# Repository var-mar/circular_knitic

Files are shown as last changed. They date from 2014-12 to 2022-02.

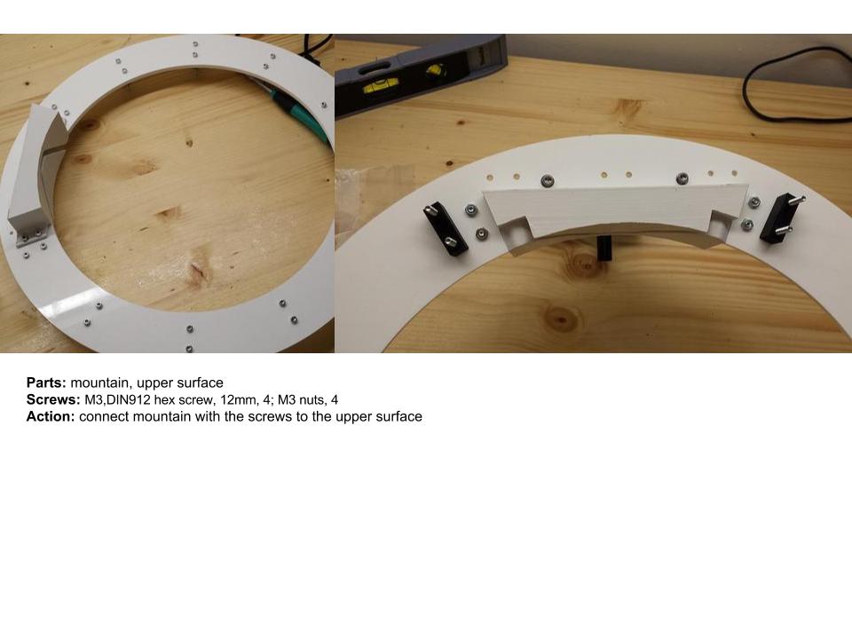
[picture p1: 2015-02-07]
workshop/CircularKniticTutorial/1.2 CK.jpg

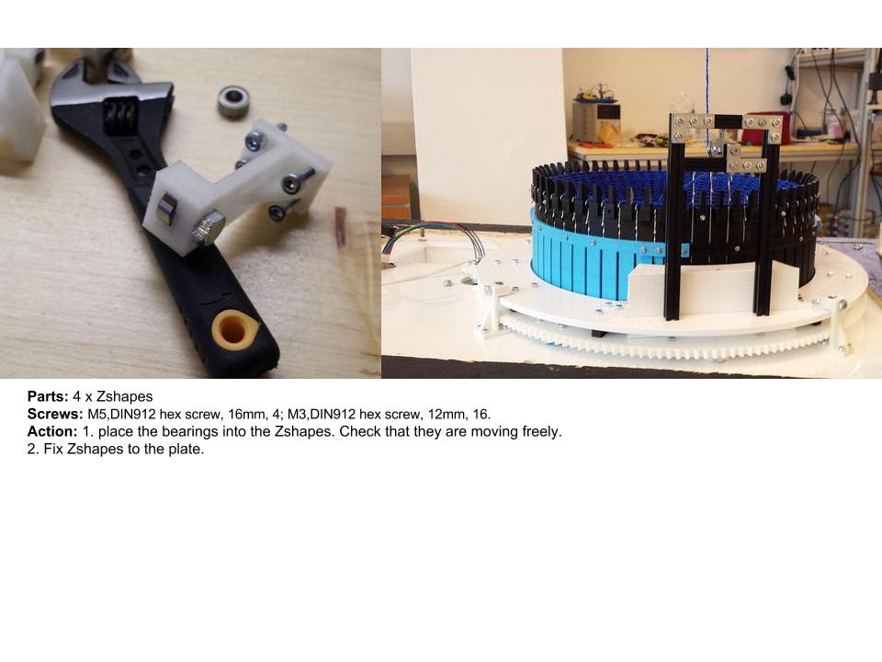
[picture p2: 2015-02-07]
workshop/CircularKniticTutorial/2.5 CK.jpg

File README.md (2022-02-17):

Circular knitic
===============

Circular Knitic, an open hardware knitting machine made by artist duo Varvara & Mar.  
* Project: https://var-mar.info/circular-knitic/ 
* Project video: https://www.youtube.com/watch?v=-GFXAGRynNM
* Instructables manual: www.instructables.com/id/Circular-Knitic/
* Manual with all pieces: http://issuu.com/marcanet/docs/circular_knitic_documentation

Brief history: This machine was done for the DOERS exhibition curated by David Cuartielles in Etopia Center for Art & Technology. We did an art intervention with 5 Circular Knitic machines, which were knitting for the time of the show (8 months). Hence, slowly the ceiling of art centre were covered with knitted tube garments. Each machine was knitting in different colour invading the exhibition space.

When building the machine, it is crucial to have the parts 3D printed precisely. Hence, print the parts in High Quality.
We have printed our machine with Ultimaker2, Makerbot Replicator 2, Makerbot Replicator 2x, and RepRapBcn+. Since reprap is not so preciase, some STL files are names as ...REP, which we have altered for that printer.

For laser cutting we have used 5mm and 6mm plexiglass. Use 6mm one for the gears, file gear-up.ai. For the rest use 5mm plexiglass. Important note, all plates are 600mm to 400mm, check you have select mm as unit. 

We are doing workshops to build one or more machines in one day, if you are interested hosting a workshop please let us know:
varvarag@gmail.com  or mar.canet@gmail.com See photos from WeMake Milano Makerspace workshop done in February 2015: https://www.flickr.com/photos/mcanet/sets/72157650274803049/

If you want to make a donation you can do in our PayPal account: varvarag@gmail.com 

To cite use:
```
@software{guljajeva_varvara_2014_6124168,
  author       = {Guljajeva, Varvara and
                  Canet Sola, Mar},
  title        = {Circular Knitic},
  month        = nov,
  year         = 2014,
  note         = {If you use this repository project, please cite it as below.},
  publisher    = {Zenodo},
  version      = {1.0.0},
  doi          = {10.5281/zenodo.6124168},
  url          = {https://doi.org/10.5281/zenodo.6124168}
}
```

We have publish some articles about this topic:
- Knitic - The Revolution of Soft Digital Fabrication. DH 2013: 497-499 [http://dh2013.unl.edu/abstracts/ab-173.html]

Opensourceecology had design some parts of the machine in parametric design in openscad:
https://wiki.opensourceecology.org/wiki/CircularKnitic_Parametric

Please send a photo if you build one machine to us we happy to make a gallery to all machines produced and a map with locations.

Copyright (c) 2014 Varvara Guljajeva & Mar Canet 

> THIS MATERIAL IS DISTRIBUTED AS IS WITH NO GUARANTEE OF FUNCTIONALITY OR RELEVANCE TO THIRD PARTY PROJECTS - THE DEVELOPERS ARE THUS NOT TO BE HELD RESPONSIBLE FOR PERSONAL INJURIES, HARDWARE, FINANCIAL, OR ANY OTHER LOSSES AND IN GENERAL FOR ANY MISFORTUNATE EVENT CAUSED BY THE DESCRIBED SOFTWARE/HARDWARE OR IN THE PROCESS OF ATTEMPTING TO IMPLEMENT IT. IF YOU DON'T AGREE WITH THE AFOREMENTIONED YOUR ARE NOT ALLOWED TO USE THE MATERIAL PROVIDED HEREIN

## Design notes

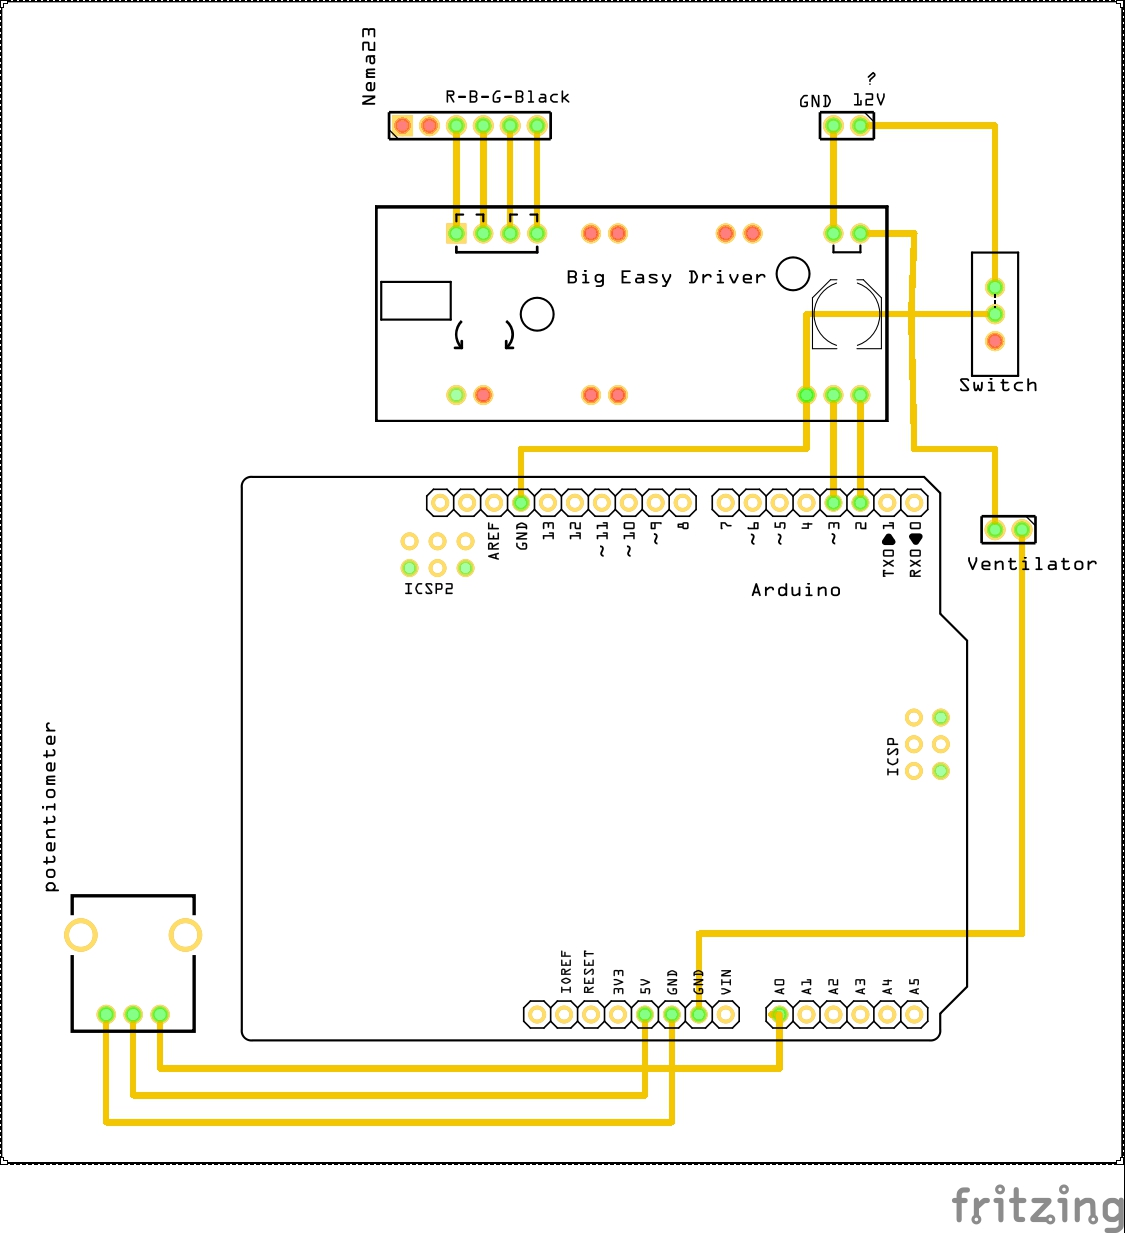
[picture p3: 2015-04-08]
Arduino/CKcircuitSchema_pcb.jpg

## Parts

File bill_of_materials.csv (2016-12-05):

Budget - Circular Knitic
description | real price | quantity | total | link
needles | €0.45 | 100 | €45.00 | http://www.bsk.co.uk/knitmastersilver-reed-sk120--sr120-xkn8-763-p.asp
stepper motor nema23 | €50.00 | 1 | €50.00
Big Easy stepper motor Driver | €20.00 | 1 | €20.00
Arduino Uno | €21.00 | 1 | €21.00
ventilator 12v 40mm x 40mm | €6.00 | 1 | €6.00
power supply 12v | €20.00 | 1 | €20.00
cabling | €8.00 | 1 | €8.00
carbon fiber tensor 2mm | €1.00 | 1 | €1.00 | http://www.mwmaterialsworld.com/es/barra-fibra-de-carbono.html
bearings (bore 5mm x 10mm x 4mm) | €0.60 | 14 | €8.40
screws and nuts | €10.00 | 1 | €10.00
shaft of motor | €7.00 | 1 | €7.00 | http://www.pololu.com/product/2675
switch | €4.00 | 1 | €4.00
paper clips | €0.01 | 30 | €0.30
Plexiglas 5mm | €10.00 | 2 | €20.00 | http://proplastik.ee
Plexiglas 6mm | €11.00 | 1 | €11.00 | http://proplastik.ee
filament | €38.00 | 1 | €38.00
makerbeam 150mm | €2.20 | 2 | €4.40
makerbeam 60mm | €0.80 | 3 | €0.80
makerbeam screws | €3.00 | 1 | €3.00
makerbeam Lshape | €0.90 | 5 | €4.50
wood structure | €25.00 | 1 | €25.00
claw weight | €6.00 | 4 | €24.00
paraphine | €2.00 | 1 | €2.00
 |  | Total | €334.00
Manufacturing
3d prints outers | €15.00 | 4 | €60.00
3d print inners | €6.00 | 24 | €144.00
3d print yarnholders | €12.00 | 4 | €48.00
3d print bearring holders | €3.00 | 5.00 | €15.00
3d print connectors | €1.00 | 15 | €15.00
Lasercutting | €90.00 | 0.5 | €45.00
 |  | Total | €327.00

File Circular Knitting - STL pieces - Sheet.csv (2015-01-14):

comments | max layer height | Order nr. | Components | # of Pieces
1 and 2 are the same pieces. | 0.06 (recommended) | 1 | BearringBig1212 (repaired).stl | 1
this piece has been made slightly bigger for the reprap printer | 0.15 | 2 | BearringBigREP (repaired).stl | 1
 | 0.06 | 3 | BearringSmall1312 (repaired).stl | 4
 | 0.15 | 4 | Pipe (repaired).stl | 1
 | 0.15 | 5 | YarnHolderPalo.stl | 2
6 and 7 are the same | 0.06 | 6 | Zshape1212 (repaired).stl | 4
made for reprap | 0.15 | 7 | ZshapeRep (repaired).stl | 4
 | 0.1 | 8 | connection0912.stl | 11
 | 0.06 | 9 | inner0112 (repaired).stl | 12
 | 0.1 | 10 | mountain1212 (repaired).stl | 1
 | 0.15 | 11 | outer2511 (repaired).stl | 4
 | 0.1 | 12 | outerNeedleConnector (repaired).stl | 4
 | 0.1 | 13 | yarnHolder0212 (repaired).stl | 4
*print all parts in 'High Quality' (the option that your slicr program has).
Max layer height 0.1mm and infill 15% or 20%.
With layer height 0.06 no filing is required

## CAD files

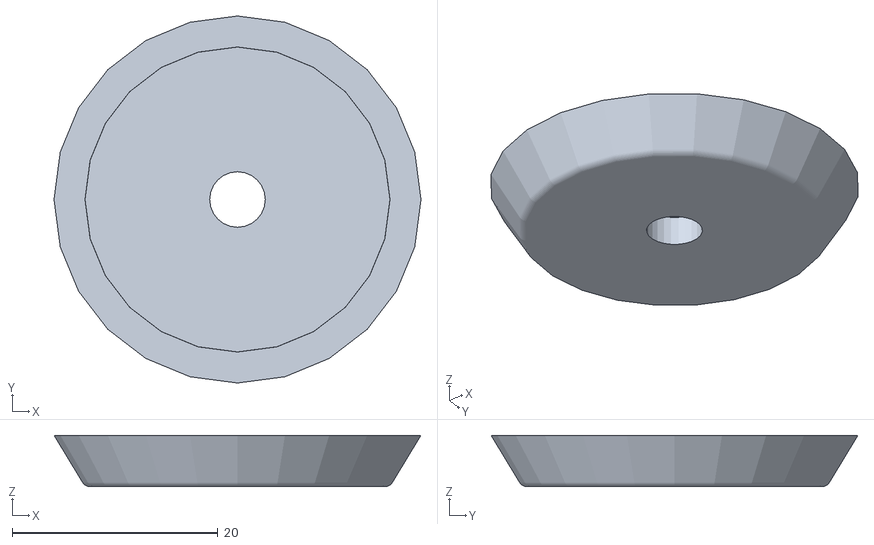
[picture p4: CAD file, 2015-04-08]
STLs/YarnTensioner/spring.stl
35.7 x 35.7 x 5.00

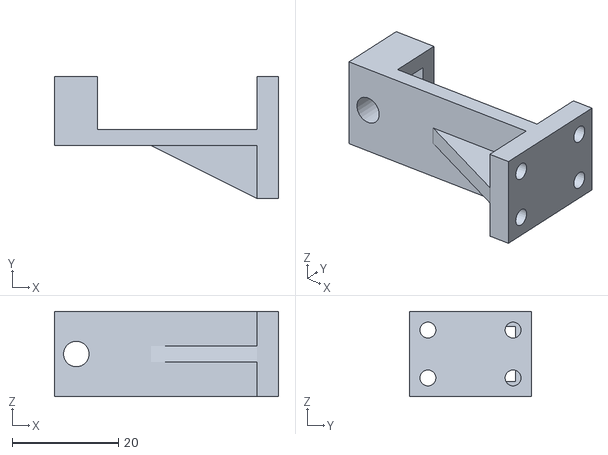
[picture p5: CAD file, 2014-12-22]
STLs/ZshapeRep_x_4.stl
42.1 x 23.0 x 16.0

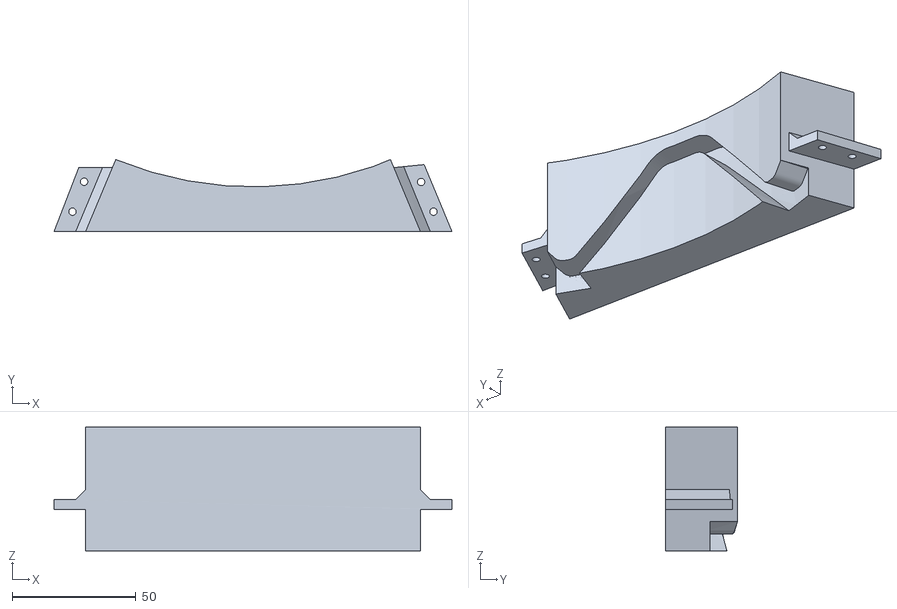
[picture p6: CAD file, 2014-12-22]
STLs/mountain1212 (repaired).stl
160.9 x 29.1 x 50.0

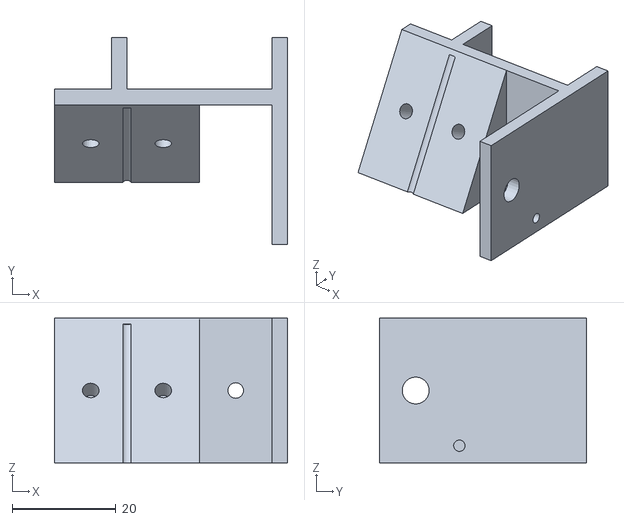
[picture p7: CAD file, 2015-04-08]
STLs/YarnTensioner/yarnfeederSupport.stl
45.0 x 40.0 x 28.0

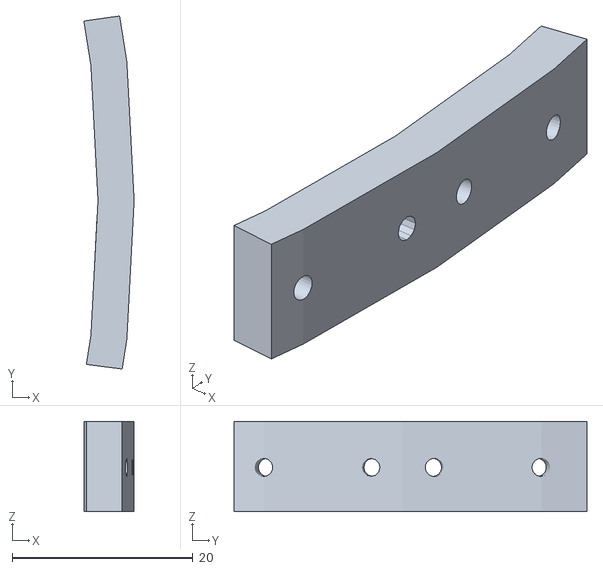
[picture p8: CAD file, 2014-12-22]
STLs/outerConnector_x_4.stl
5.57 x 39.1 x 10.0

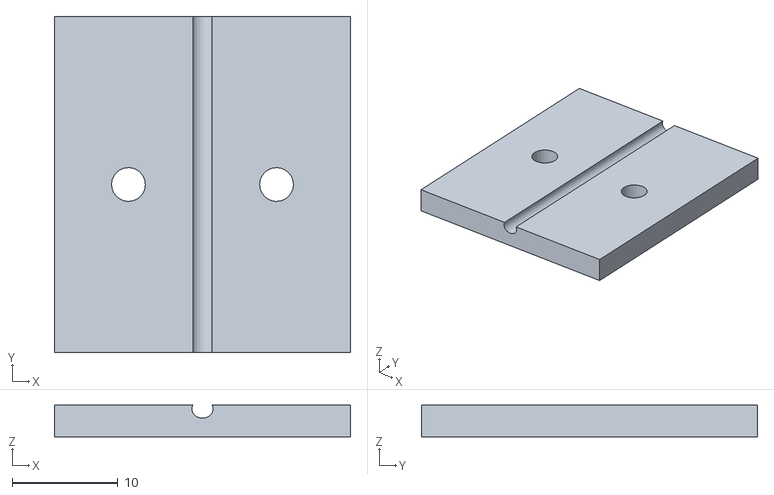
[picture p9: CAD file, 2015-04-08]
STLs/YarnTensioner/YarnTensonerHolder300315.stl
28.0 x 31.8 x 3.00

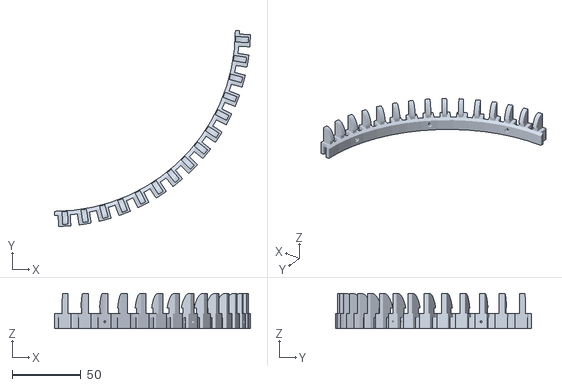
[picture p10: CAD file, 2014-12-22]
STLs/yarnHolder0212_x_4.stl
142.9 x 142.9 x 25.6

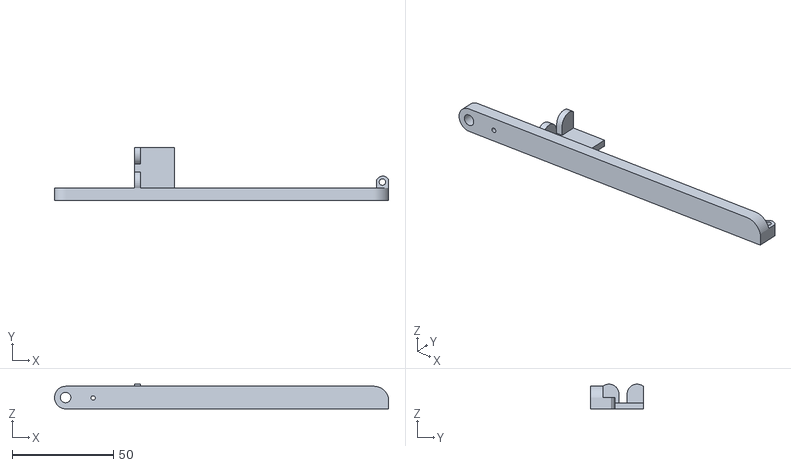
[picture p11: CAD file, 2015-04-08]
STLs/YarnTensioner/yarnTensioner1.stl
165.3 x 26.0 x 12.3

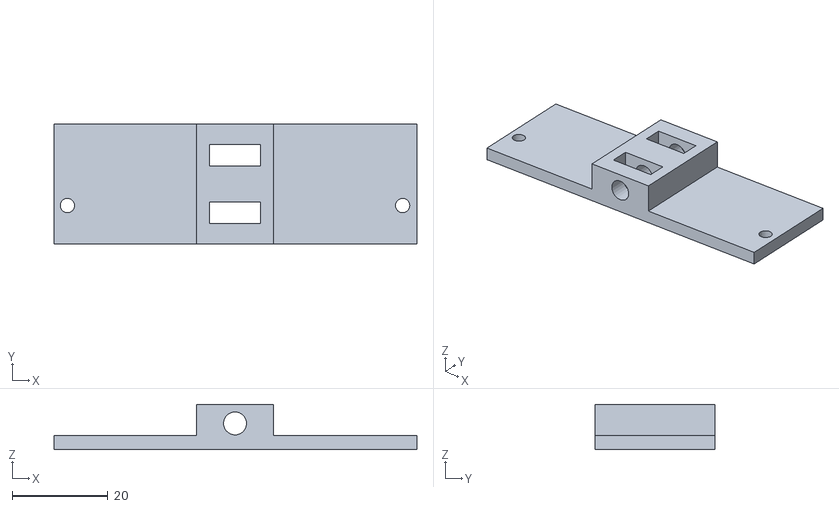
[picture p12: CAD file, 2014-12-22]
STLs/BearringBigREP (repaired).stl
75.8 x 25.0 x 9.50

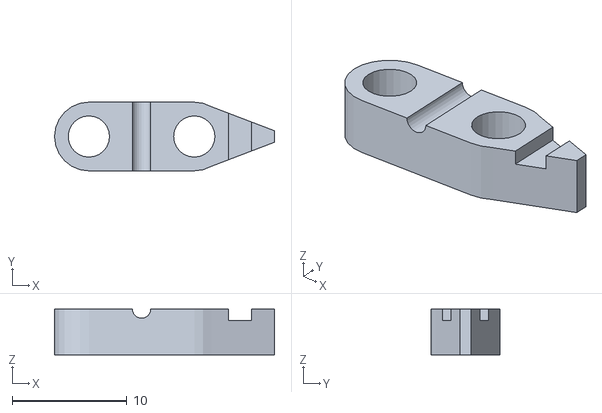
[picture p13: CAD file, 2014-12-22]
STLs/YarnTensioner/YarnHolderPalo.stl
19.2 x 6.00 x 4.00

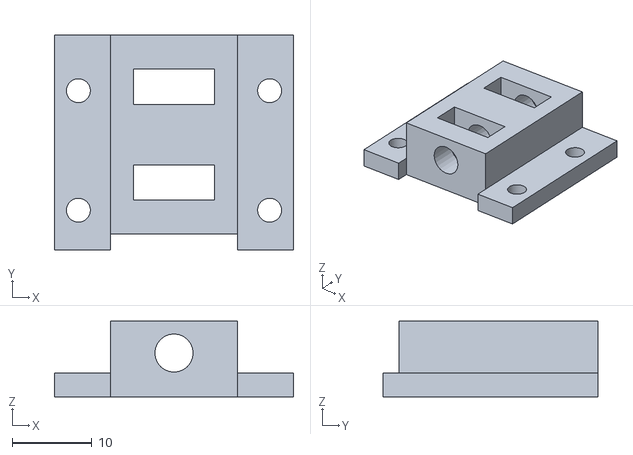
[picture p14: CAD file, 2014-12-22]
STLs/BearringSmall1312_x_4.stl
30.0 x 27.0 x 9.50

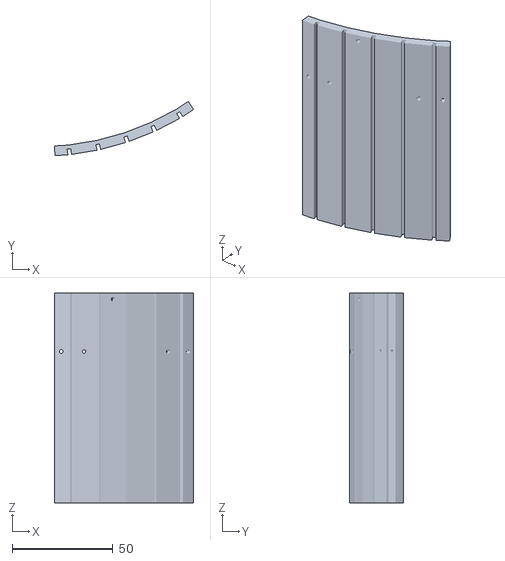
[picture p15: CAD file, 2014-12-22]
STLs/inner0112_x_12.stl
69.0 x 26.8 x 104.0

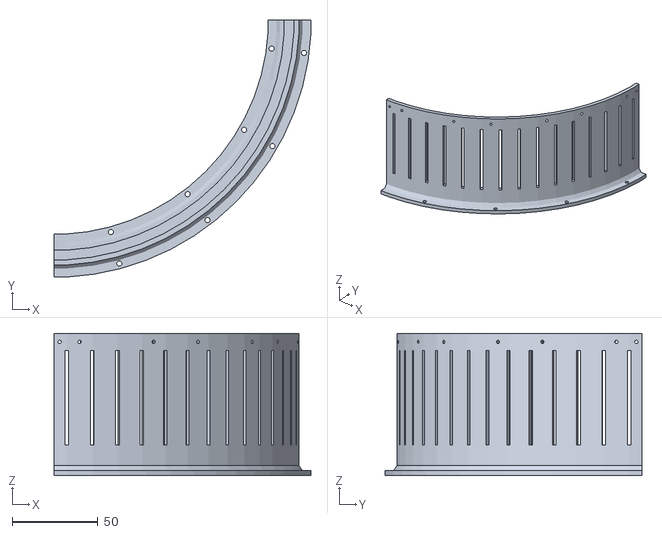
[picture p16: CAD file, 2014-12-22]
STLs/outer2511_x_4.stl
149.8 x 149.8 x 83.0

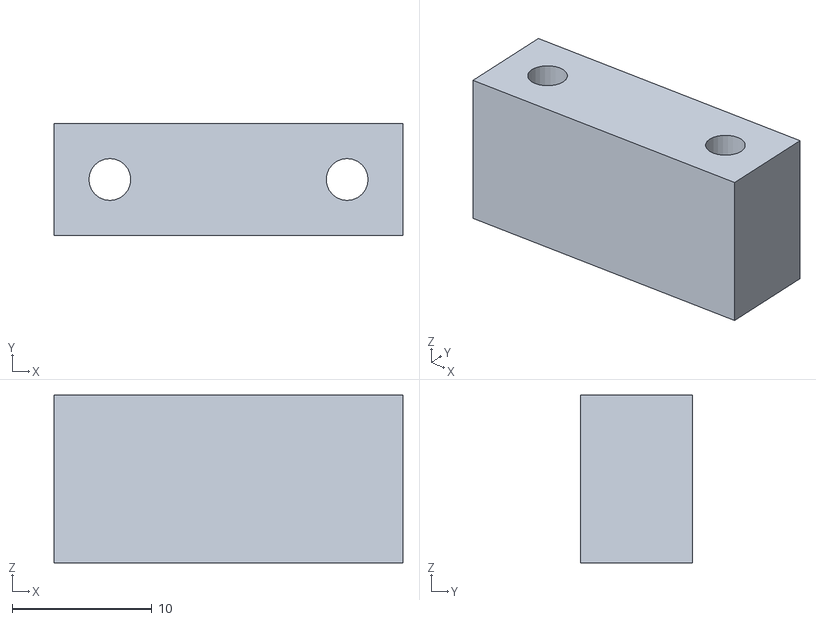
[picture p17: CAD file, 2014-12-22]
STLs/connection0912_x_11.stl
25.0 x 8.00 x 12.0

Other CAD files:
STLs/BearringBig1212 (repaired).stl
STLs/Zshape1212_x_4.stl
3D_model/CircularKnitic~.skp

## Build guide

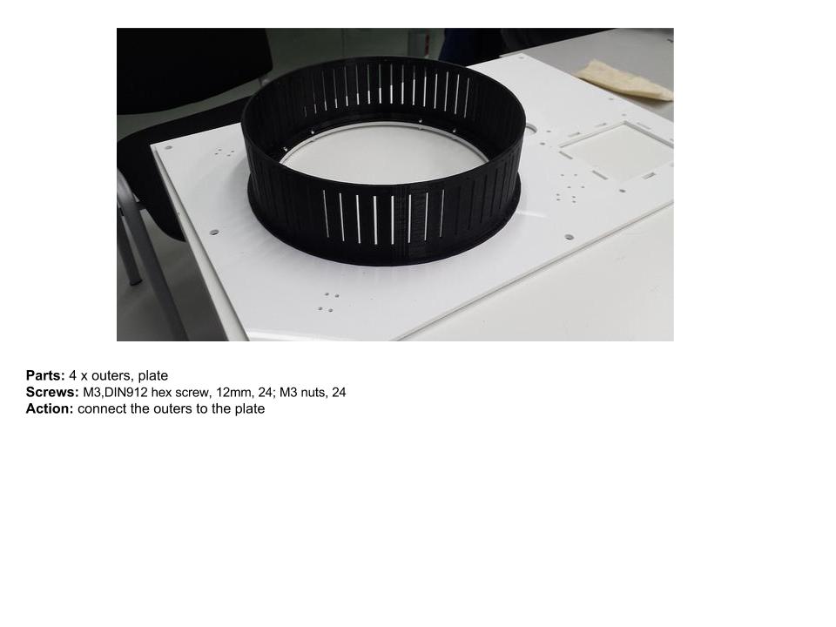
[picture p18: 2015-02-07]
workshop/CircularKniticTutorial/2.1 CK.jpg

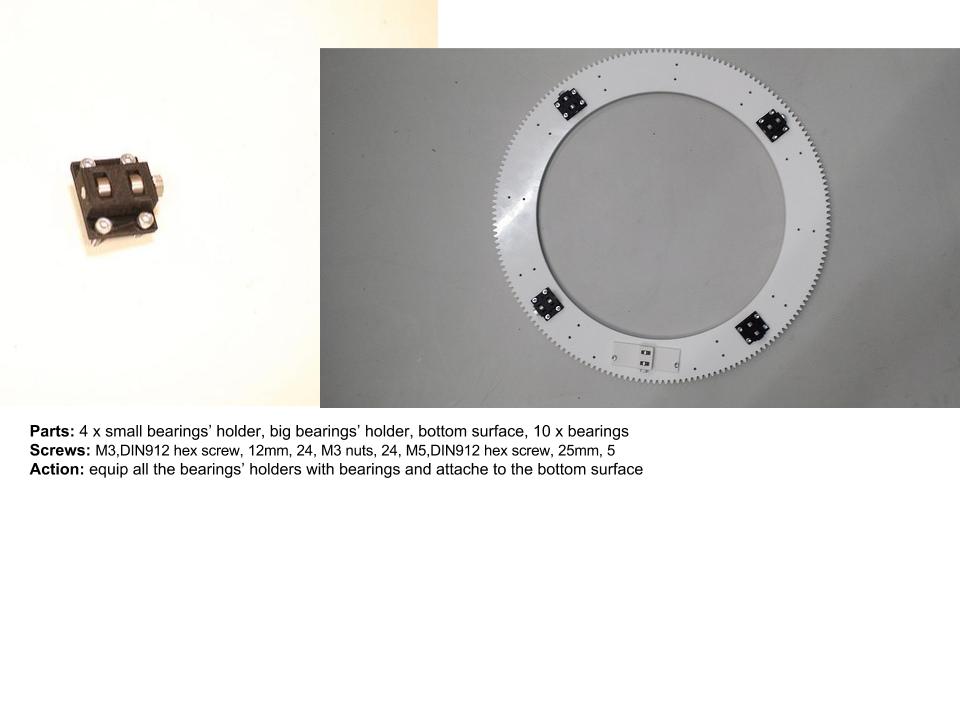
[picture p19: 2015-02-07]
workshop/CircularKniticTutorial/2.2 CK.jpg

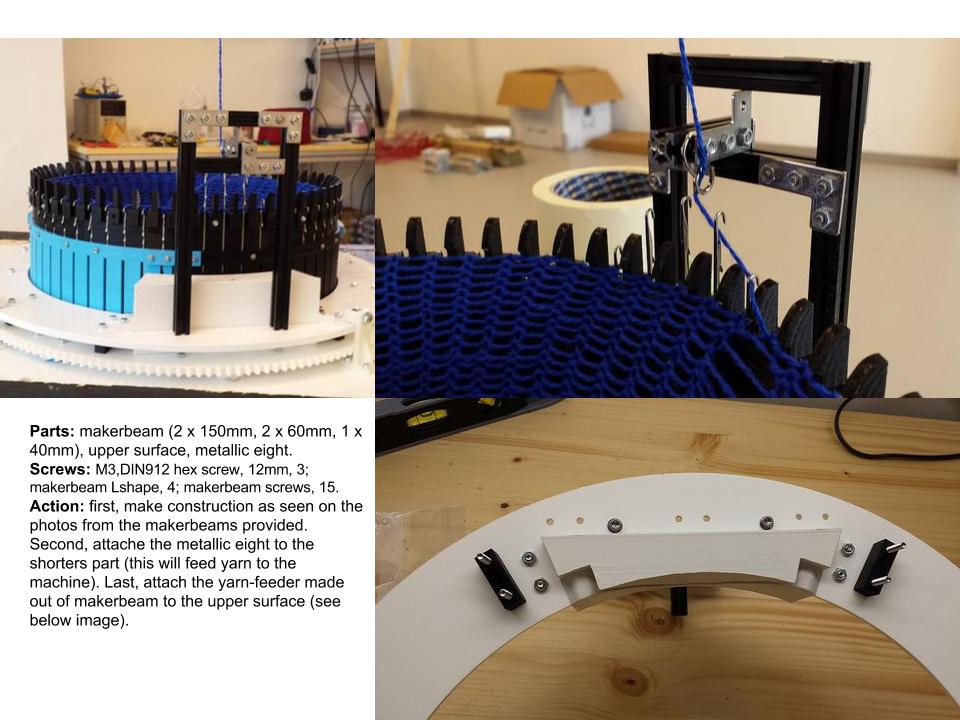
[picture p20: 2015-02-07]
workshop/CircularKniticTutorial/1.3 CK.jpg

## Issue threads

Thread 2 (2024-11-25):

Questions About Circular Knitic

serrarrs, 2024-11-25:
Hi Varvara and Mar,

I’m a master’s student at Hochschule Pforzheim in the Design and Future Making department, and as part of one of my projects, I’m working on creating the Circular Knitic. I have a few questions regarding the 3D printing and laser-cutting of some parts:

-Regarding the 3D printing, I noticed that the required layer height is quite thin, which significantly increases the printing time. Could you explain why such thin layers are necessary for this project?

-For the laser-cutting process, is there a specific offset value I should consider to achieve the correct thickness for the cuts?

-Lastly, about the plexiglass parts: can I use the same thickness (5mm) for all the components, or are there any specific parts that require a different thickness?

Thank you very much for your time and support :)
Best regards,
Serra

oujlaki, 2024-11-25:
hi!!
We are also students at the Free University of Bolzano, faculty of design and we have seen your beautiful project as a reference for our knitting machine. We are looking for the right needles. Could you give us some additional information? we understand that they are the master silver reed sk120 sr120, but I can't find them in the right size online.
waiting for your kind help,
best regards
karola

mcanet, 2024-12-04:
Hi,

The needle type is well-documented (Silver Reed SK120, SR120 LATCH NEEDLES 8mm). While other needle types can be used, they may require adaptations in the design. This particular needle is not the most common, but it is available for purchase on eBay or other platforms.
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
Screen shot from our manual: https://issuu.com/marcanet/docs/circular_knitic_documentation

High-precision 3D printing with a small layer height is required. You can experiment with lower resolution (larger layer heights), but this will depend on your 3D printing machine. Additionally, it may require extra sanding to assemble everything properly.

All plexiglass components can also be made with 5mm thickness.

We’d love to see photos if you build it!

Best regards,

Mar

serrarrs, 2024-12-09:
Hi,

Thank you for your answer! Is it possible to send the link to the motor you used? There are many versions of the Nema 23 motor, and I'm not sure which one is correct.

Best,
Serra

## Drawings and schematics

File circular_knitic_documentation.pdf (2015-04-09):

open source knitting machine
http://var-mar.info | http://www.knitic.com

Varvara Guljajeva & Mar Canet

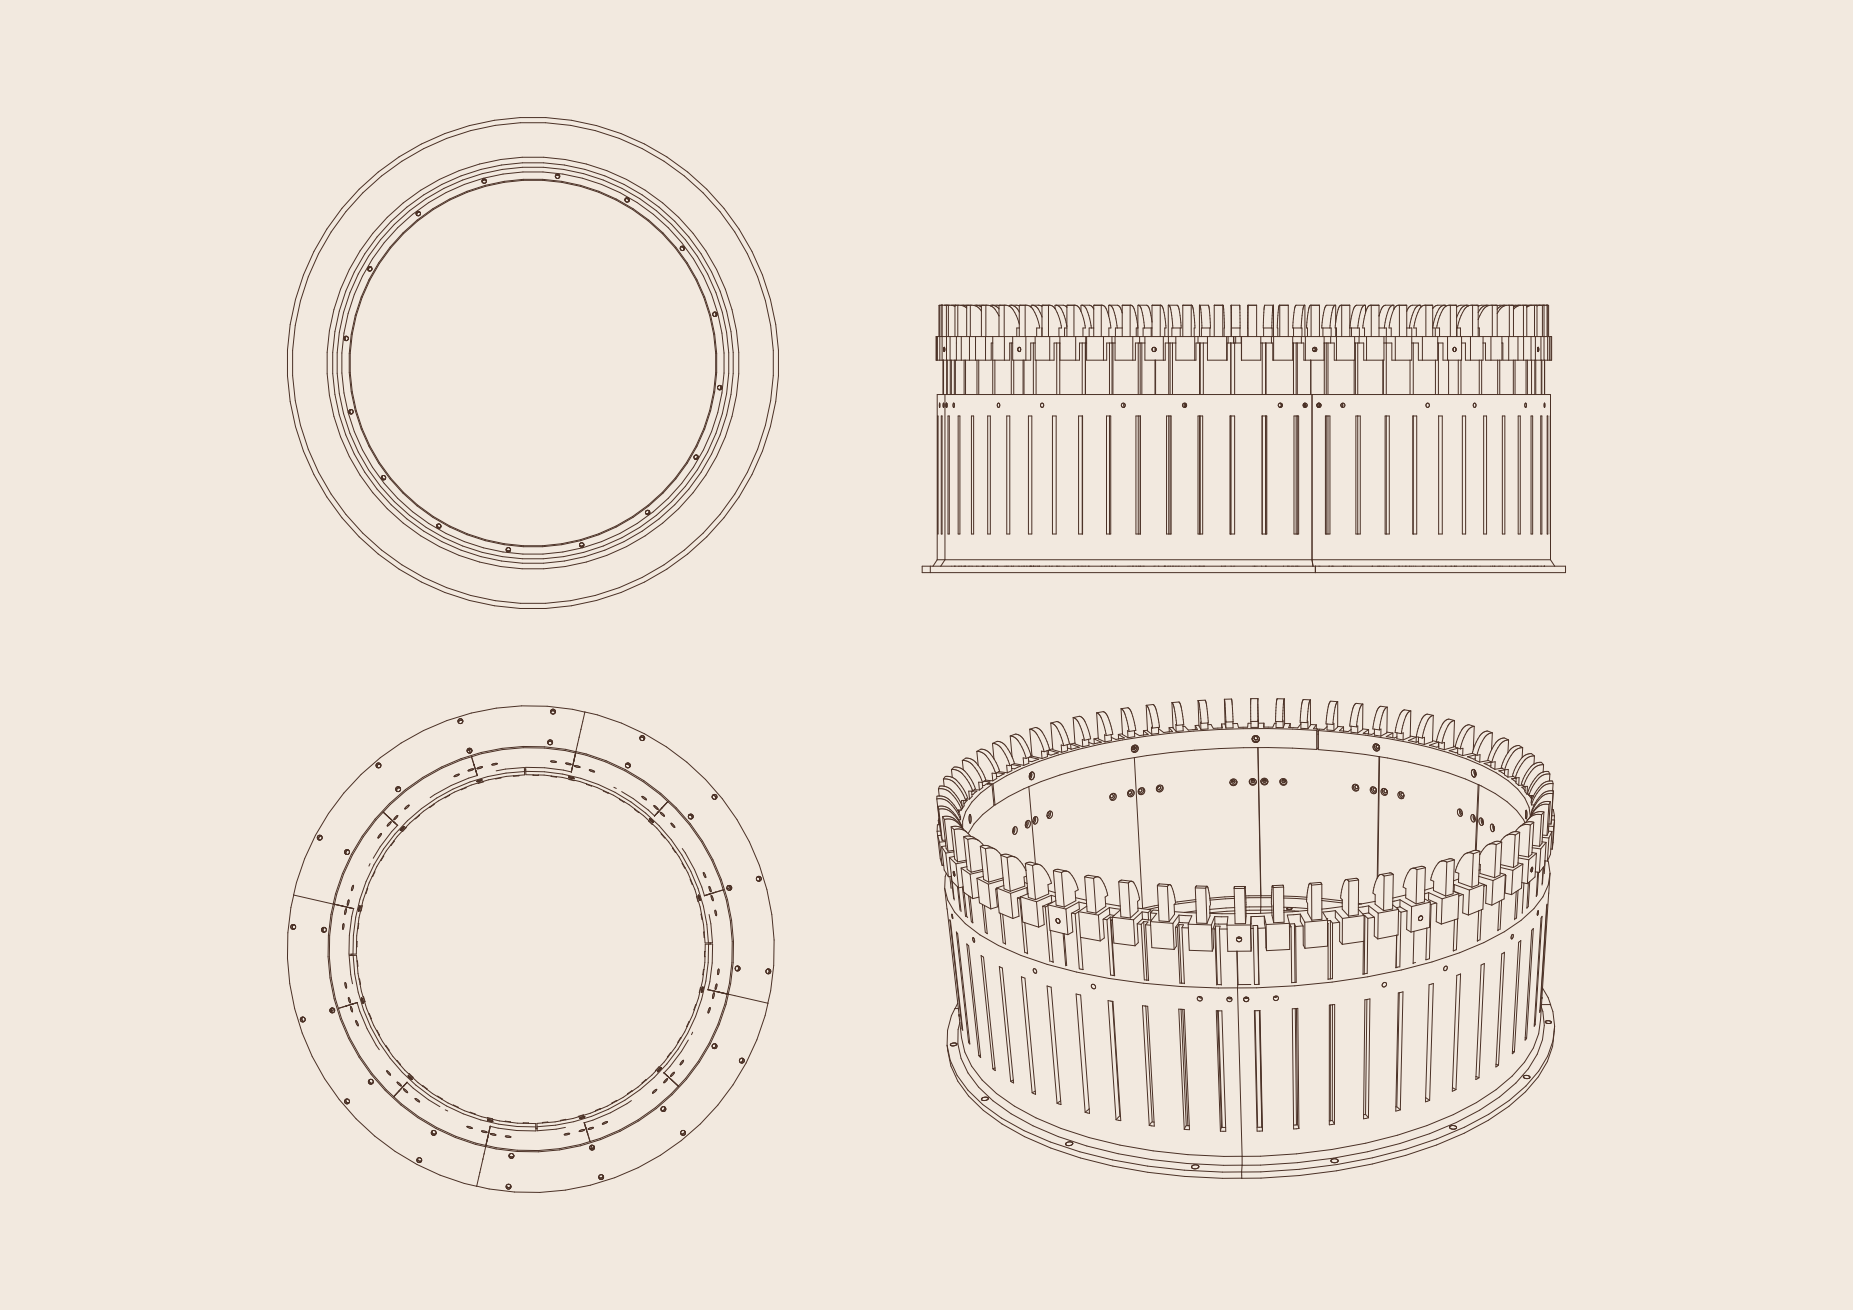
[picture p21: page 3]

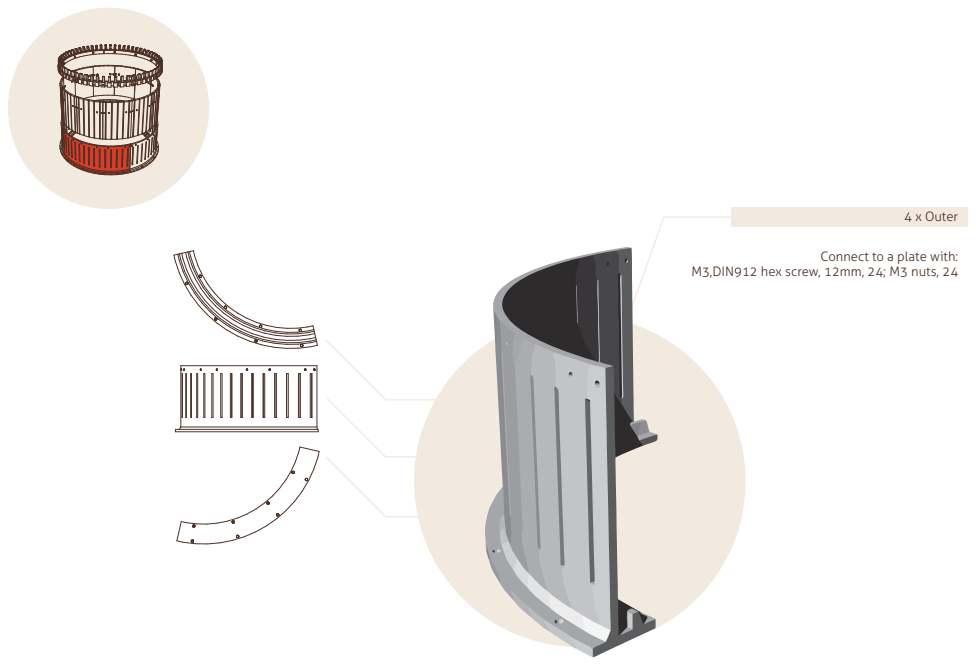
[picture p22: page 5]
4 x Outer

Connect to a plate with:

M3,DIN912 hex screw, 12mm, 24; M3 nuts, 24

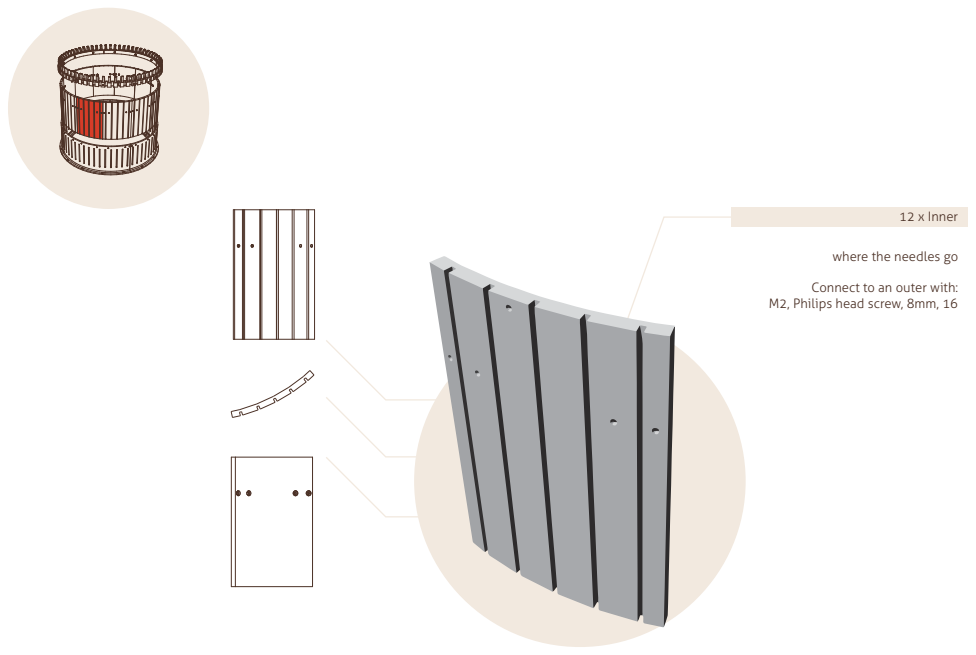
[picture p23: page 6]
12 x Inner

where the needles go

Connect to an outer with:
M2, Philips head screw, 8mm, 16

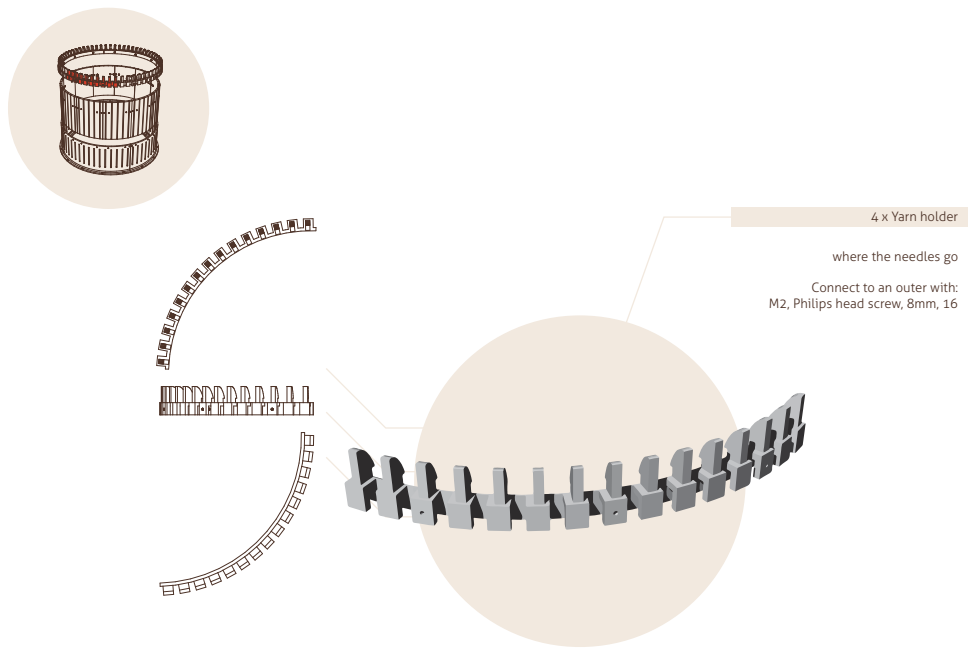
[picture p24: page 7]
4 x Yarn holder

where the needles go

Connect to an outer with:
M2, Philips head screw, 8mm, 16

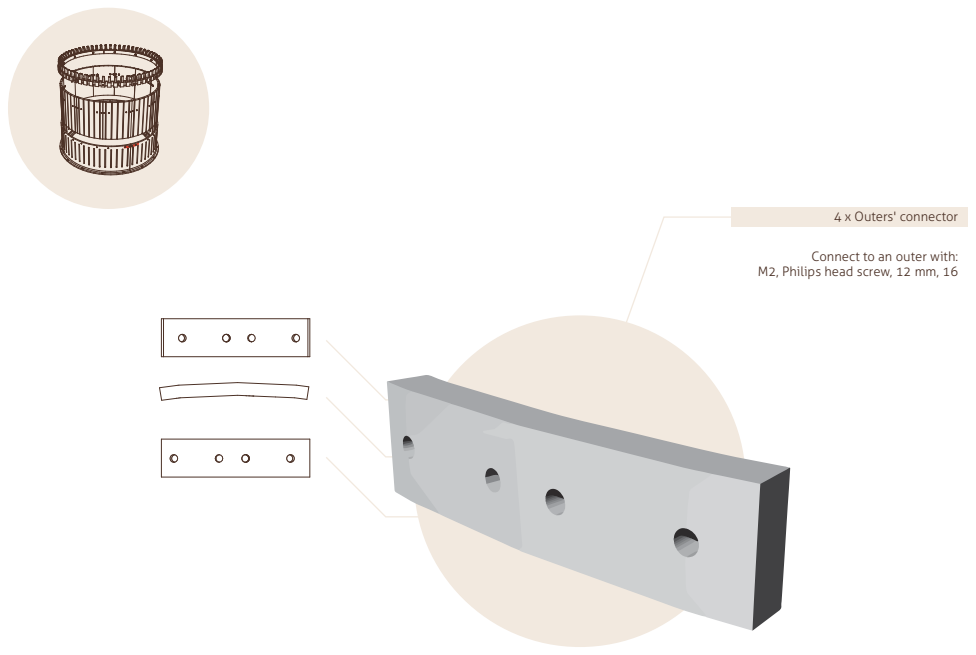
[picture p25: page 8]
4 x Outers' connector

Connect to an outer with:

M2, Philips head screw, 12 mm, 16

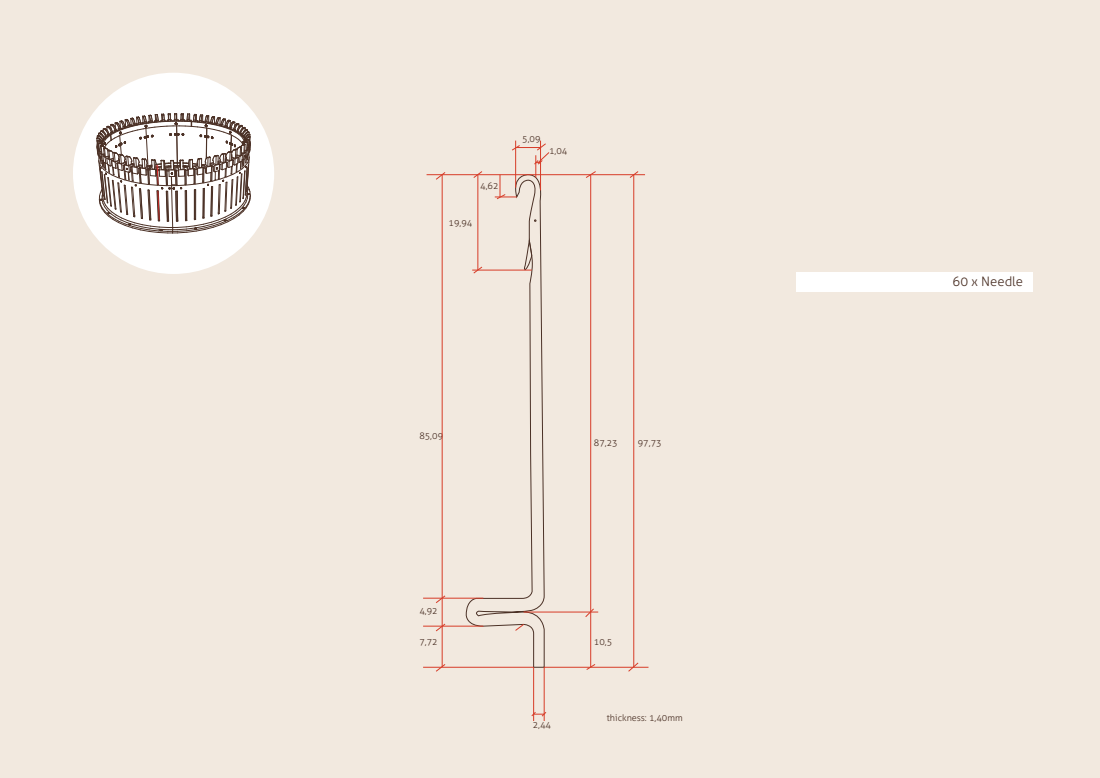
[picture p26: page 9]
60 x Needle; thickness: 1,40mm

Bottom surface (big gear) + motor gears

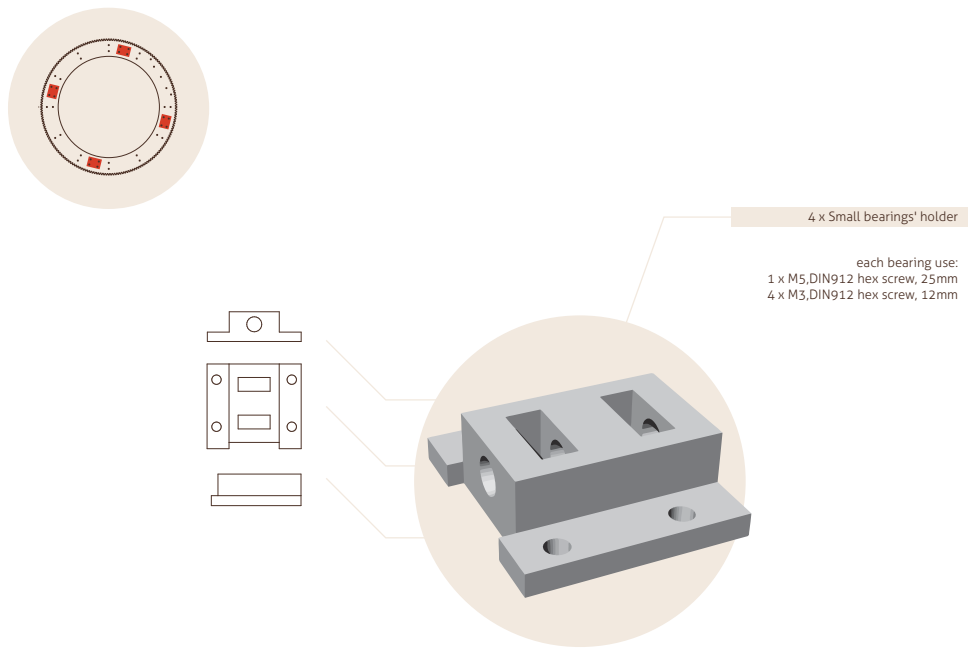
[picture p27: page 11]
1 x M5,DIN912 hex screw, 25mm 4 x M3,DIN912 hex screw, 12mm

4 x Small bearings' holder

each bearing use:

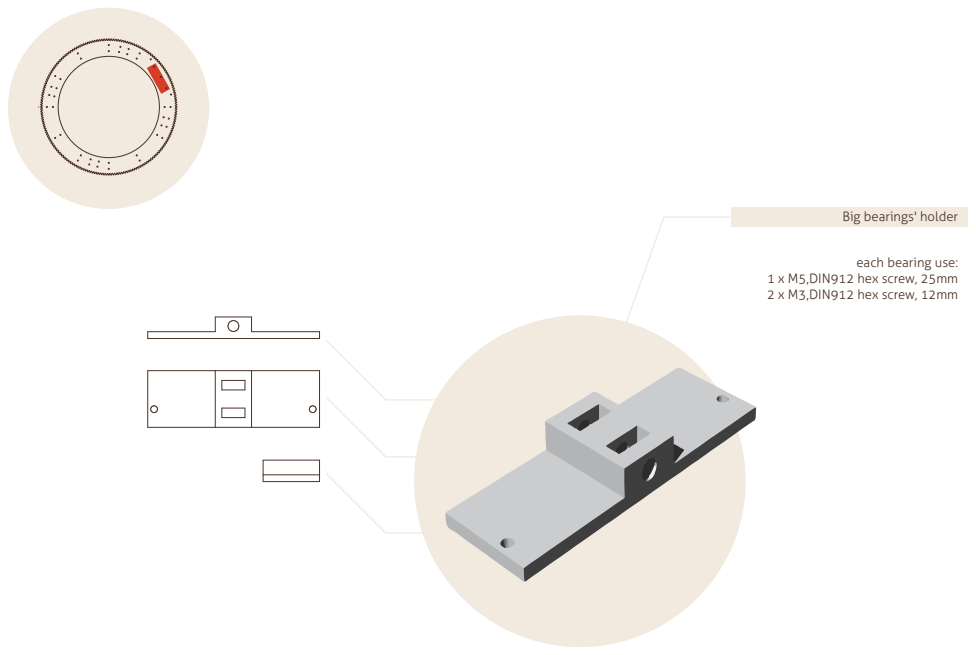
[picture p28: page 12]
1 x M5,DIN912 hex screw, 25mm 2 x M3,DIN912 hex screw, 12mm

Big bearings' holder

each bearing use:

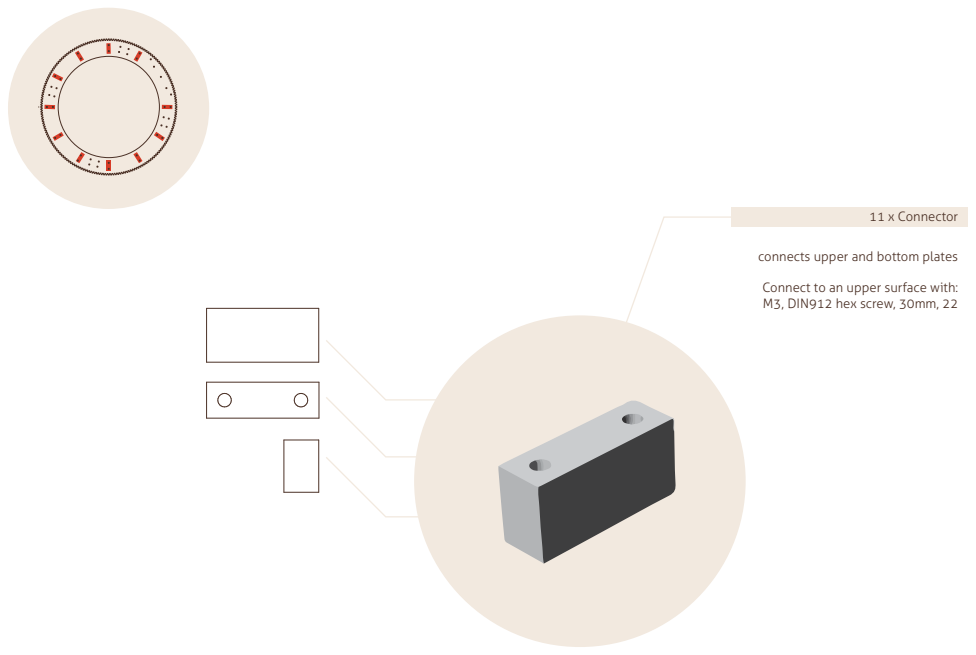
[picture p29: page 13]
11 x Connector

connects upper and bottom plates

Connect to an upper surface with:
M3, DIN912 hex screw, 30mm, 22

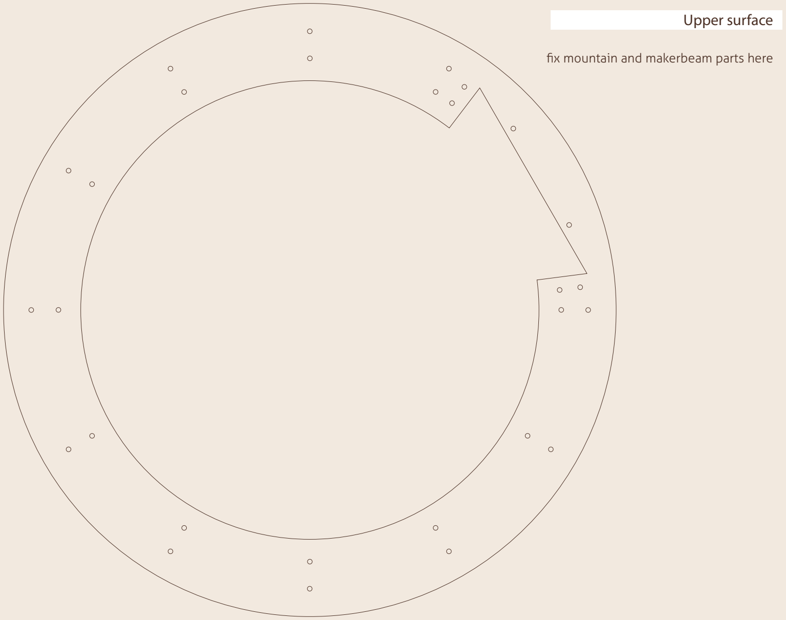
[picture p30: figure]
fix mountain and makerbeam parts here; Upper surface
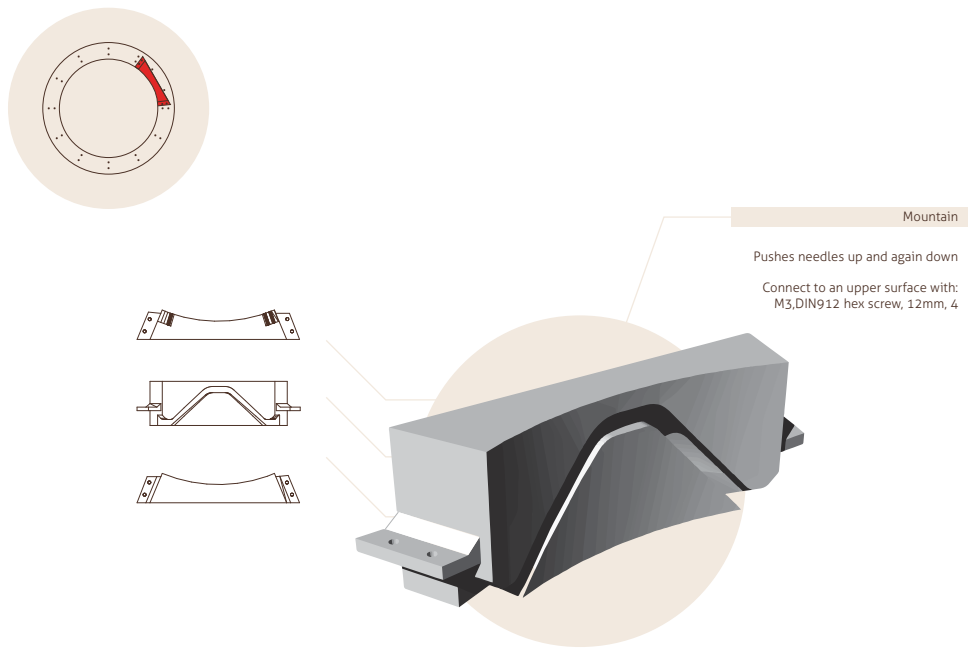
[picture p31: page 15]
Mountain

Pushes needles up and again down

Connect to an upper surface with:
M3,DIN912 hex screw, 12mm, 4

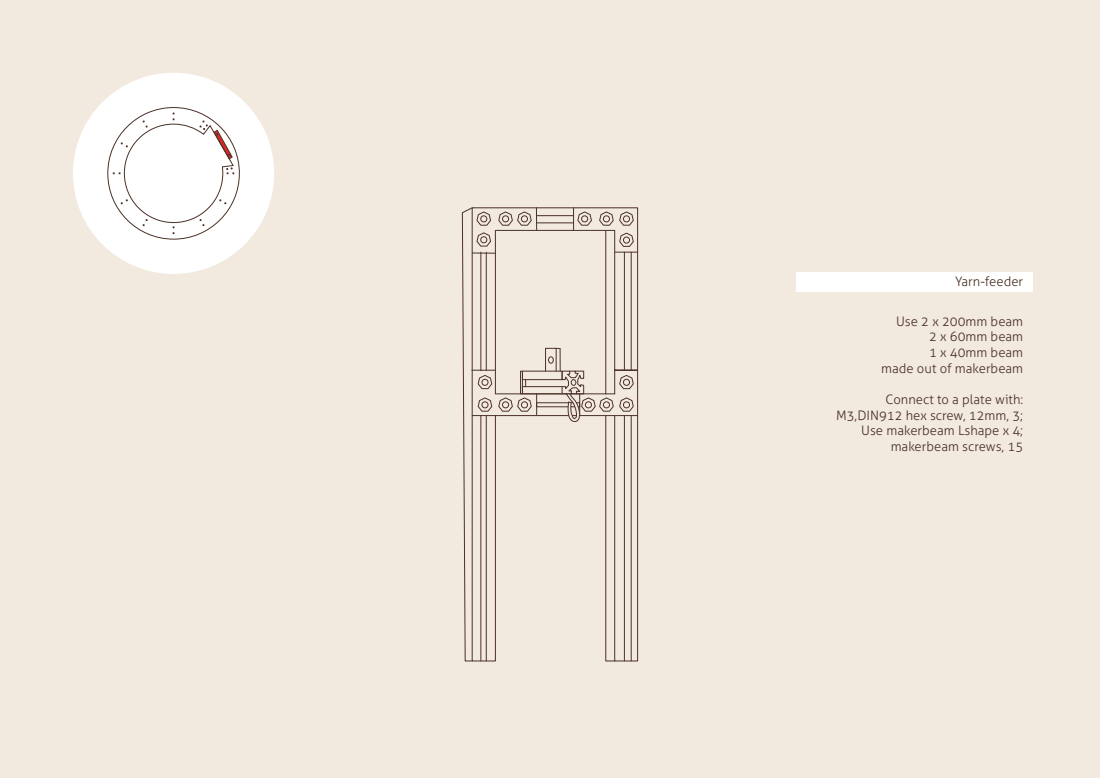
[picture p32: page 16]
Use 2 x 200mm beam 2 x 60mm beam 1 x 40mm beam; Yarn-feeder

made out of makerbeam

Connect to a plate with:

M3,DIN912 hex screw, 12mm, 3;
Use makerbeam Lshape x 4;
makerbeam screws, 15

Plate nema23

here will be mounted all the machine parts

M5,DIN912 hex screw, 16mm, 4.; M3,DIN912 hex screw, 12mm, 16; 4 x Z-shape

keeps the surfaces down and doesn't

allow to move them up

Place a bearing with:

Connect to a plate with:

M6, hex screw, 70mm, 4

Box of electronics

here goes all the cables, basically: stepper motor
driver, ventilator, switch, potentiometer, arduino, etc.

Put together and connect to a plate with:

Electronic schema

weight: 113g.

4 x Knitting machine claw weight

this item fixes a stick, which brings yarn

to the machine, into the table

1 x Connector

mechnism for yarn tensioner.
Connects to the structu

11 x Connector

connects upper and bottom plates

Connect to an upper surface with:
M3, DIN912 hex screw, 30mm, 22

2 x Spring

connects upper and bottom plates

Connect to an upper surface with:
M3, DIN912 hex screw, 30mm, 22

Connect with M3, 8mm, 2; 2 x Yarn holder2

Attach a metal piece for passing the yarn

Metallic eight

thickness: plate and surfaces

Bottom surface (big gear)


Circular Knitic table

### Wood parts to create the machine frame

Other parts

Screws circular Knitic

Others

Size

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
Type

Philips head screw
Philips head screw
steel nut

Screw button head socket
DIN912 hex screw

DIN912 hex screw
DIN912 hex screw
steel nut

DIN912 hex screw
DIN912 hex screw
steel nylon lock nut
Philips head

hex screw
steel nut
wing steel nut

hospa screws

metallic angle | 30x30 x 15 x 2cm | mount wood frame

Long

8mm
12 mm

6mm
12mm

16mm
30mm

16mm
25mm

50mm

70mm

20mm

Quantity

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
attach inners with outer
attach inners with outer connections, yarn holders

makerbeam
attach outers to plexi, and z-shape, small and big bearings’ holders, mountain, construction from makerbeam
attach gear on the stepper motor
attach gear wheel with spacers

attach stepper motor
attach bearing

mount the electronic box
mount the electronic box
mount the electronic box

mount wood frame

Curated by; David Cuartielles; 20th December 2014 - 31th July 2015; Commissioned by; More info:

www.knitic.com - www.var-mar.info

Catalog design: Jesús Rodríguez

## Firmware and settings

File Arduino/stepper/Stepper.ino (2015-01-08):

int stp = 3;  //connect pin 13 to step
int dir = 2;  // connect pin 12 to dir
int stp2 = 5;  //connect pin 13 to step
int dir2 = 4;  // connect pin 12 to dir

int speedDelay = 8000;

void setup() 
{                
  pinMode(stp, OUTPUT);
  pinMode(dir, OUTPUT);
  pinMode(stp2, OUTPUT);
  pinMode(dir2, OUTPUT);  
  digitalWrite(dir, HIGH);
  digitalWrite(dir2, LOW);
  delay(100);
}


void loop() 
{
    digitalWrite(stp, HIGH); 
    digitalWrite(stp, LOW);   
    delayMicroseconds(speedDelay);   
    digitalWrite(stp2, HIGH);
    digitalWrite(stp2, LOW);
    delayMicroseconds(speedDelay);       
}

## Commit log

2014-12-22 Add STL
    [BearringBig1212 (repaired).stl, BearringBigREP (repaired).stl, BearringSmall1312 (repaired).stl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]
2015-01-08 add parts to build machine
    [CircularKnitic~.skp, bill_of_materials.csv]
2015-01-14 add STL cvs sheet
    describing how many of each one is need
    [Circular Knitting - STL pieces - Sheet.csv]
2015-01-14 fix csv
    [Circular Knitting - STL pieces - Sheet.csv]
2015-01-27 add more information to document
    add screws, and other information
2015-02-02 update arduino box plexi cut
2015-02-03 add cutting plexi plates corrected names and updated files
2015-02-03 fix red line in plate nema23
2015-02-03 fix nema 23 plate
2015-02-03 update STL parts
    [BearringSmall1312_x_4.stl, StickHolder.stl, Zshape1212_x_4.stl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]
2015-04-08 new tensioner STL model
    [yarnTensioner1.stl]
2015-04-08 Add yarn tensioner and delete yarnholderPalo
    yarn tensioner are 4 pieces
    [YarnHolderPalo.stl, YarnTensonerHolder300315.stl, spring.stl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]
2015-04-08 Add schema Arduino
2015-04-08 update yarn holder
    [StickHolder.stl, YarnHolderPalo_x_2.stl, yarnHolder0212_x_4.stl]
2015-08-14 updated yarn tensioner STL, 2d files (ai, svg)
    [YarnHolderPalo.stl, YarnTensonerHolder300315.stl, spring.stl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]
2016-12-05 makerbeam update
    Fix error
    [bill_of_materials.csv]
